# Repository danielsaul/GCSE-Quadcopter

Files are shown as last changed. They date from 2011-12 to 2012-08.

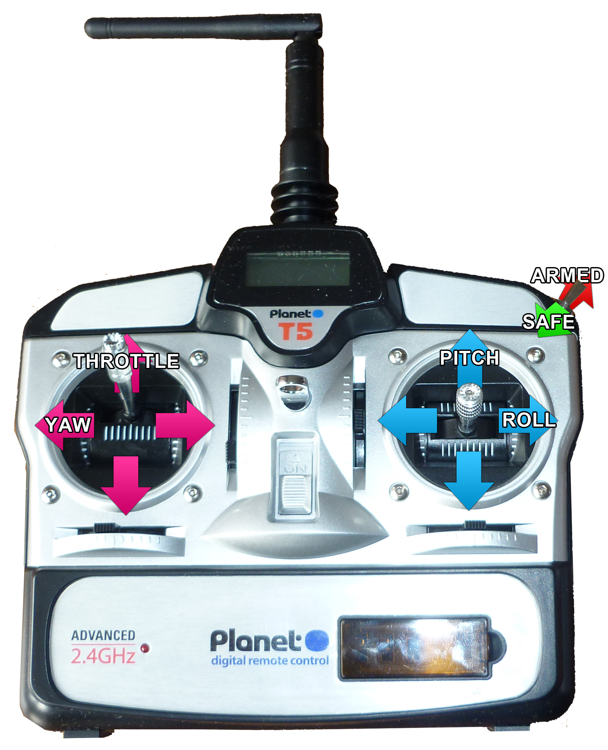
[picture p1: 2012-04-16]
Graphics/transmitterdiagram.jpg

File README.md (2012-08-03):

#GCSE Quadcopter - NOT FUNCTIONAL.
###Still here for historical purposes :)
#### � Copyright Daniel Saul

My GCSE Quadcopter project: the aim of which is to create a fully-functional, four rotored, remote control helicopter from scratch. 
Uses a custom designed PCB with an ATmega328 as the core microcontroller, using the arduino bootloader.

The IMU is made up of a 3-axis accelerometer, a 2-axis gyro and a 1-axis gyro to get 6 degrees of freedom. There is the possibility of extending this to include a magnetometer and GPS in the future.

There will also be an ultrasonic rangefinder on board for low-level altitude control.

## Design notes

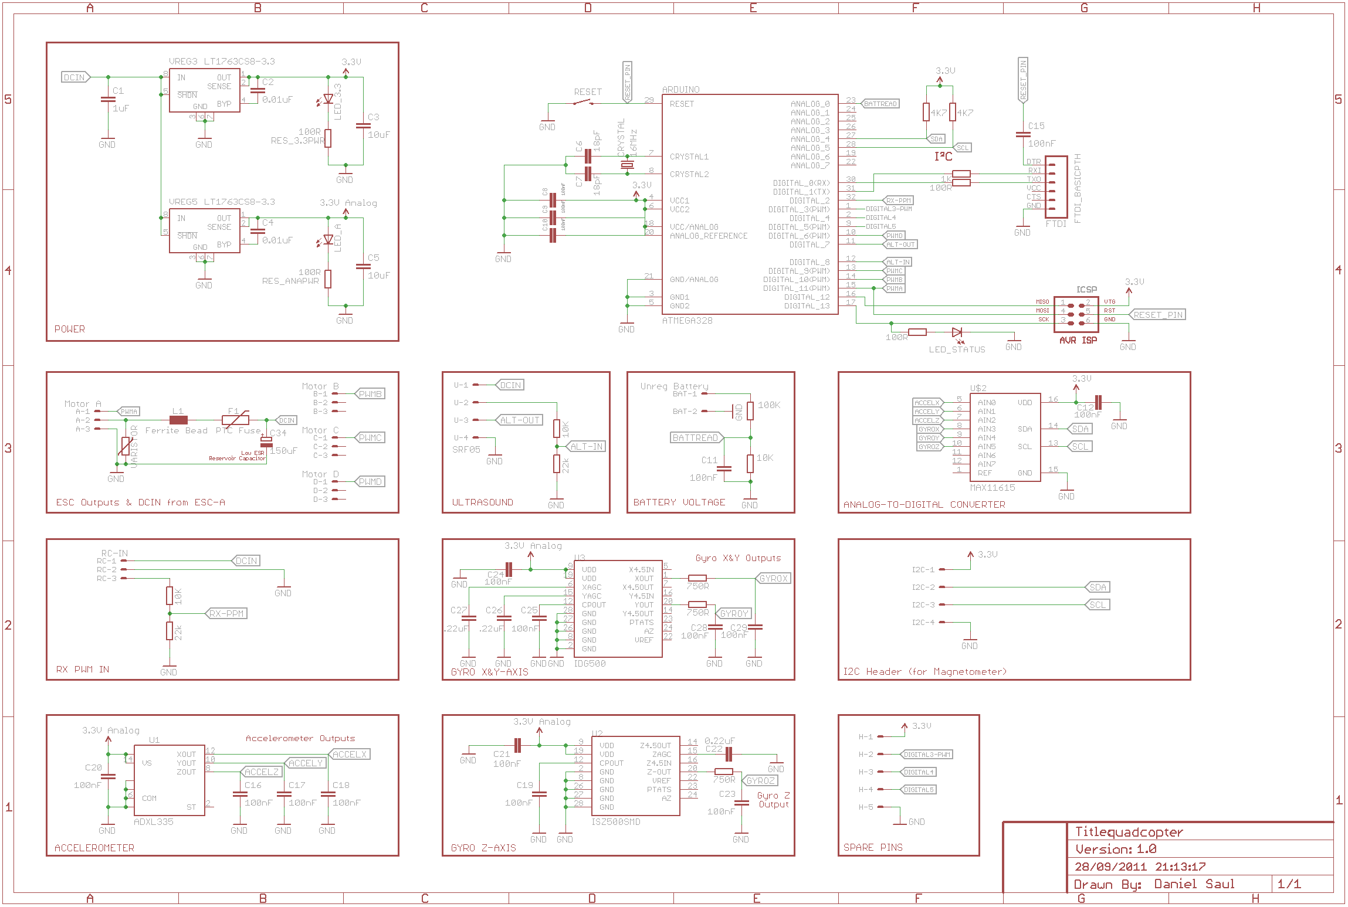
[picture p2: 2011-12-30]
PCB/schematic.png

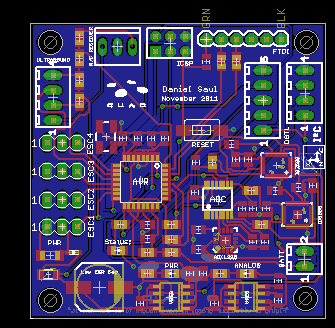
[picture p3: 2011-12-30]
PCB/pcb.png

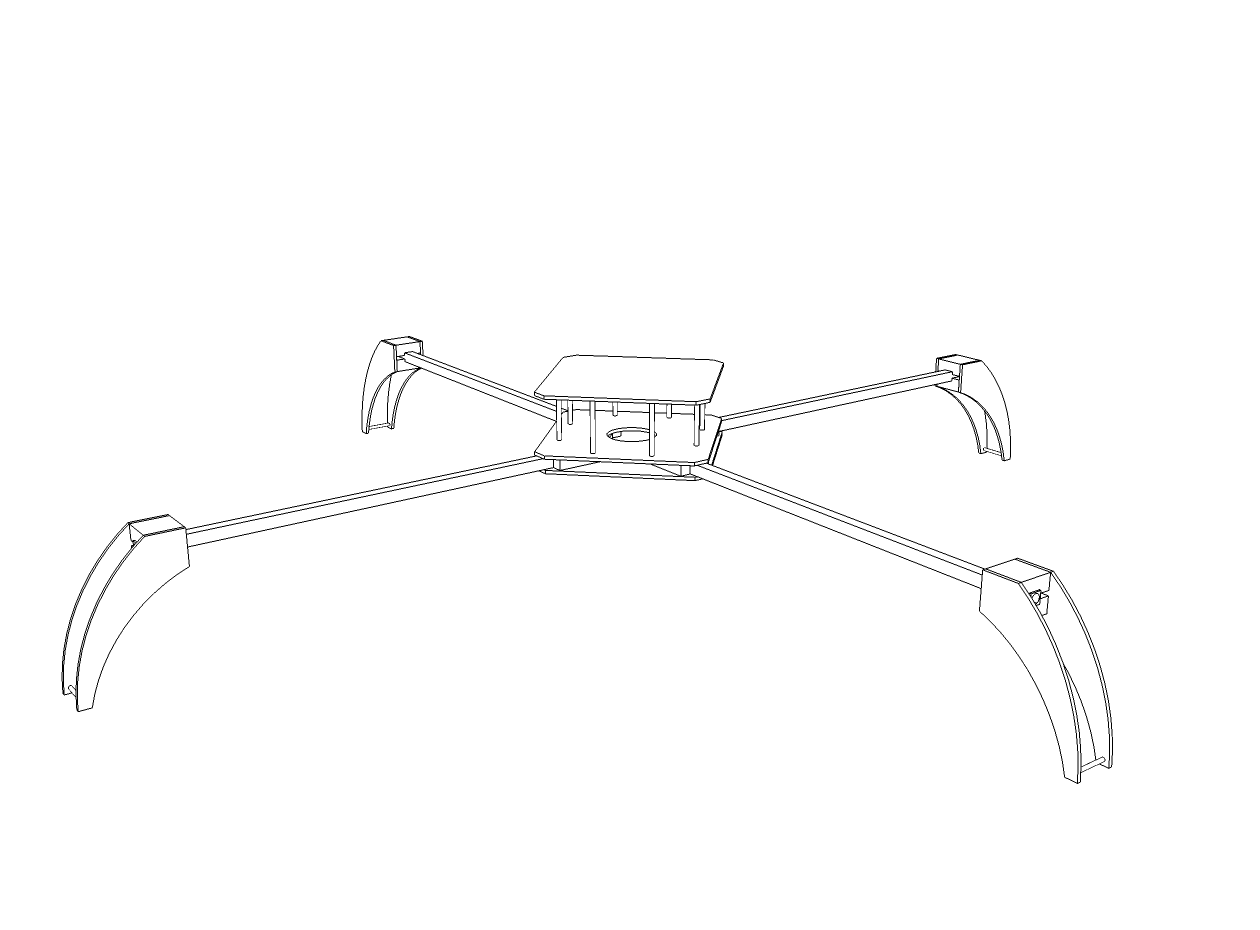
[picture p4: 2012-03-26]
Frame/line.png

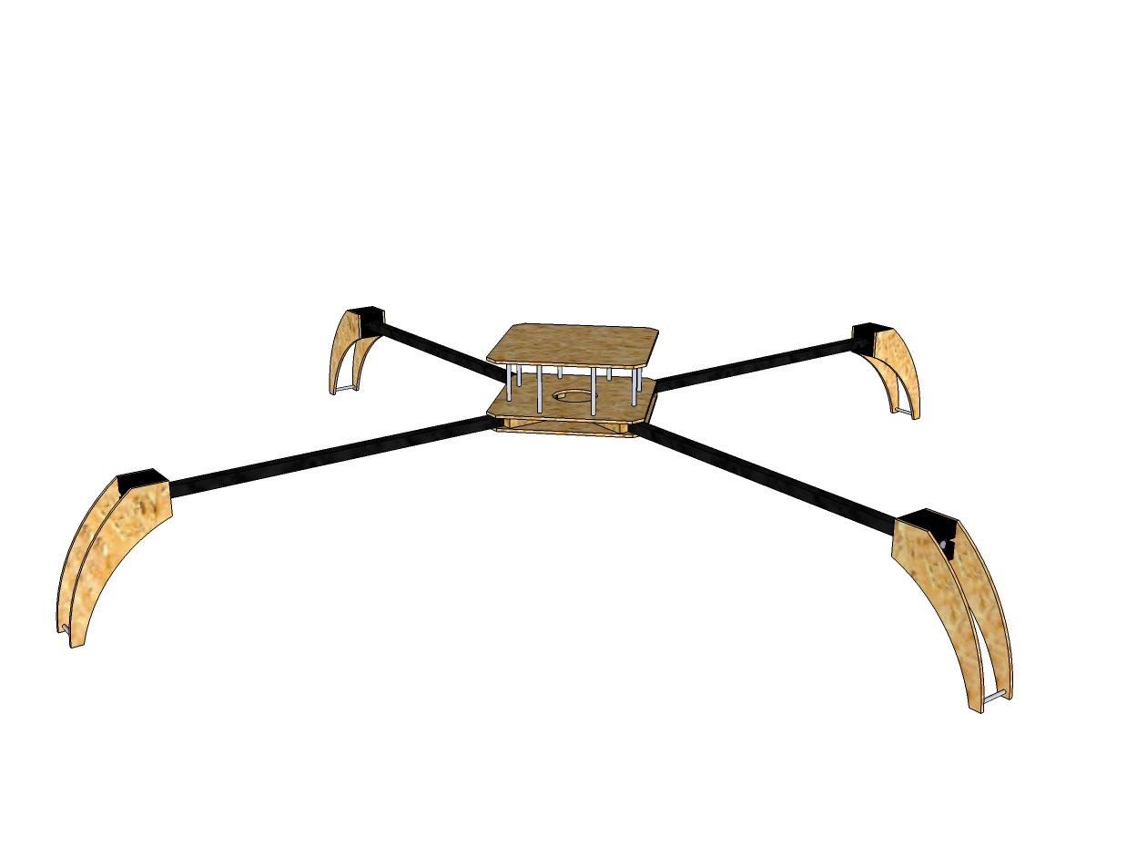
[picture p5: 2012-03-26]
Frame/shaded.png

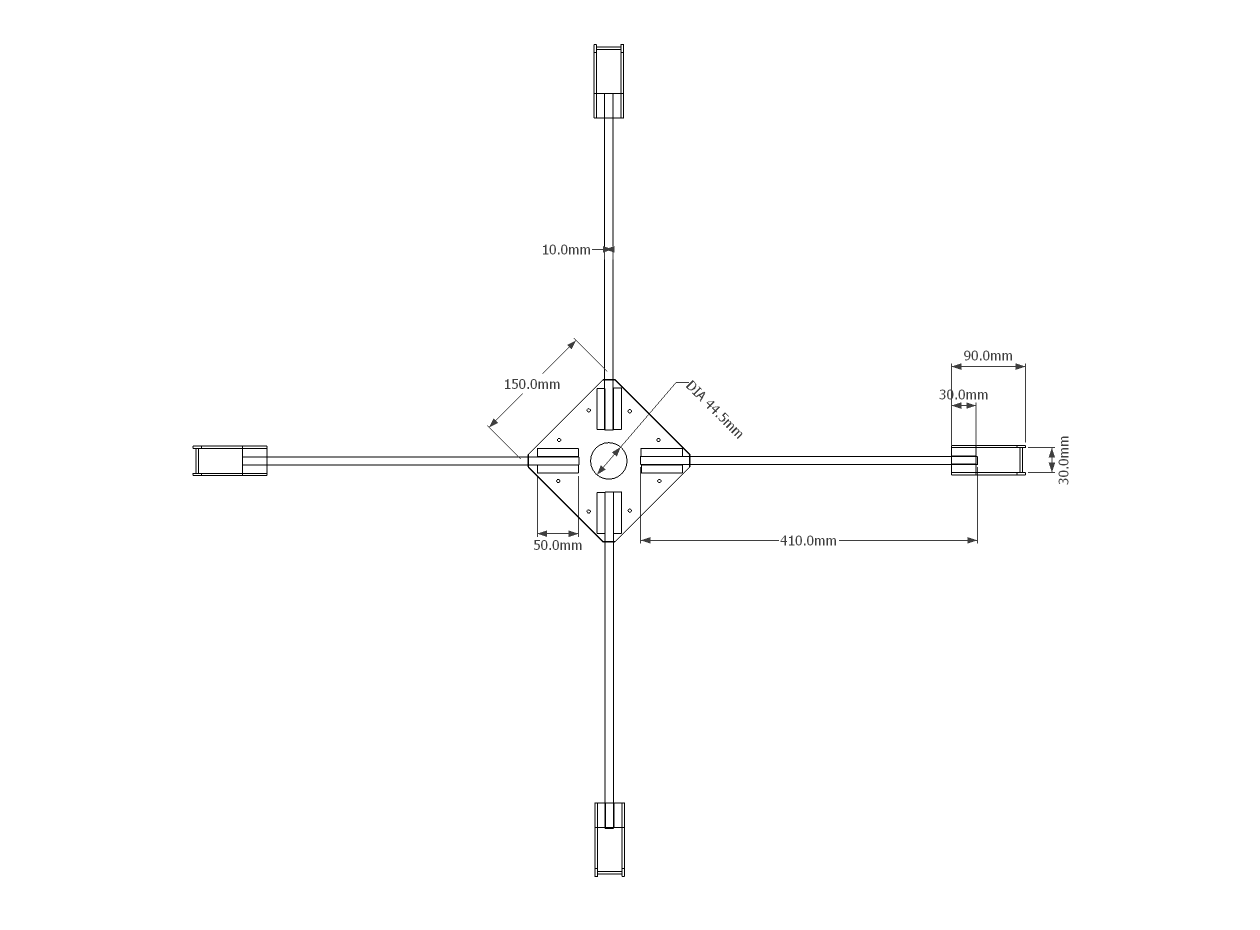
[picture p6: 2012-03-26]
Frame/line-top-dimensions.png

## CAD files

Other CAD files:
Frame/real.skp

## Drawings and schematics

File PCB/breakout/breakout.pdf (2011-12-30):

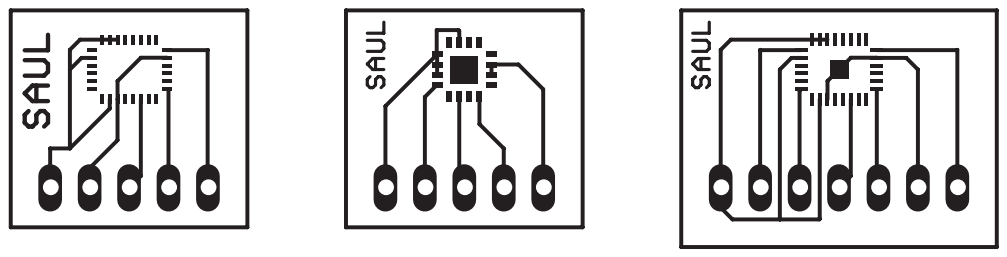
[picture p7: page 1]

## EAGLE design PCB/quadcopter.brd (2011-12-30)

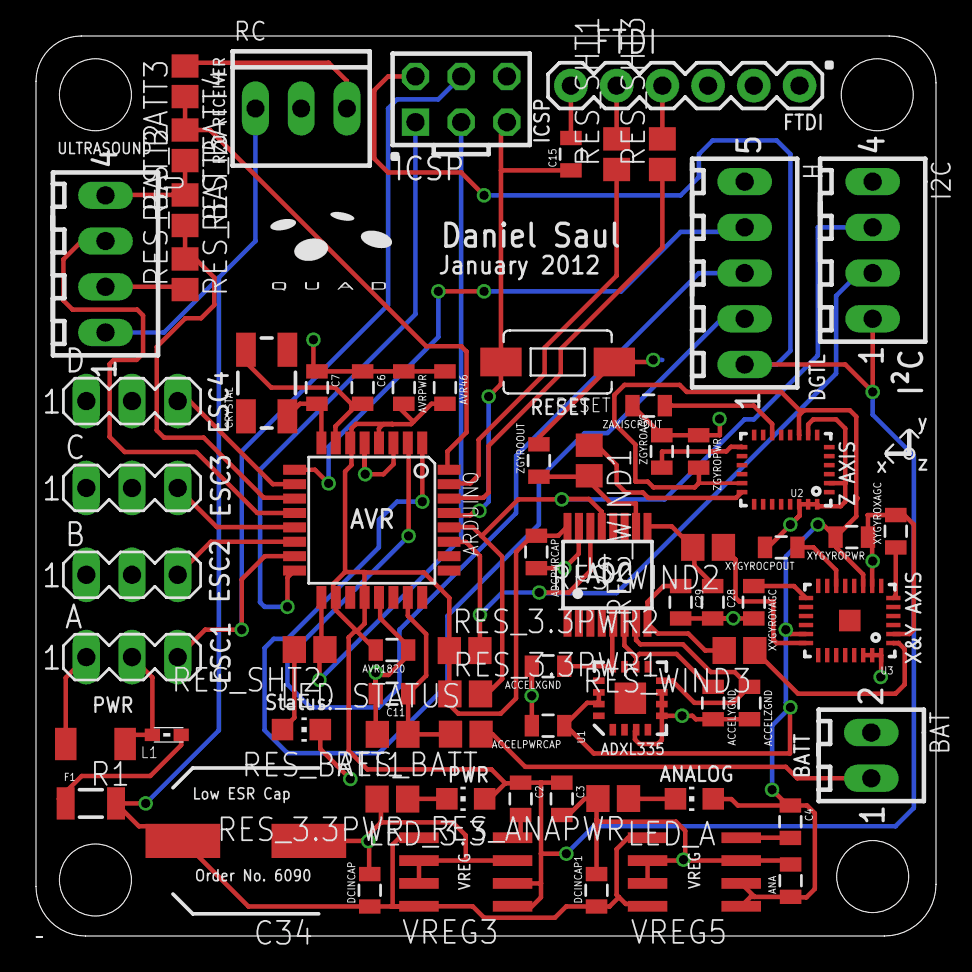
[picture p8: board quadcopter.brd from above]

Board: 2 copper layers, 50.0 x 50.0 mm, 72 parts (1 on the bottom side), 51 nets.

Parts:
A: Motor A; MA03-1
ACCELPWRCAP: 100nF; 0805
ACCELXGND: 100nF; 0805
ACCELYGND: 100nF; 0805
ACCELZGND: 100nF; 0805
ADCPWRCAP: 100nF; 0805
ANA: 10uF; 0805
ARDUINO: ATMEGA328; TQFP32-08
AVR46, AVR1820: 100nF; 0805
AVRPWR: 100nF; 0805
B: MA03-1
BAT: Unreg Battery; 6410-02
C: MA03-1
C2, C4: 0.01uF; 0805
C3: 10uF; 0805
C6, C7: 18pF; 0805
C11, C15, C28, C29: 100nF; 0805
C34: 150uF; SANYO-OSCON_SMD_E7
CRYSTAL: 16MHz; CRYSTAL-SMD-5X3
D: MA03-1
DCINCAP, DCINCAP1: 1uF; 0805
F1: PTC Fuse; PTC-1206
FTDI: FTDI_BASICPTH; FTDI_BASIC
H: 6410-05
I2C: 6410-04
ICSP: AVR-ISP-6
L1: Ferrite Bead; 0603
LED_3.3: red; CHIP-LED0805
LED_A: red; CHIP-LED0805
LED_STATUS: blue; CHIP-LED0805
R1: VARISTOR; CT/CN1206
RC: RC-IN; 22-23-2031
RESET: TACTILE-SWITCH-1101NE
RES_3.3PWR: 100R; R0805
RES_3.3PWR1, RES_3.3PWR2: 4K7; R0805
RES_ANAPWR: 100R; R0805
RES_BATT: 100K; R0805
RES_BATT1, RES_BATT2, RES_BATT4: 10K; R0805
RES_BATT3, RES_BATT5: 22k; R0805
RES_SHT1: 1K; R0805
RES_SHT2, RES_SHT3: 100R; R0805
RES_WIND1, RES_WIND2, RES_WIND3: 750R; R0805
U: SRF05; 6410-04
U1: ADXL335; LFCSP-16
U2: ISZ500SMD; QFN-28_6X8
U3: IDG500; SPARKFUN_IDG500
U$1: LOGO
U$2: MAX11615; QSOP16
VREG3, VREG5: LT1763CS8-3.3; SOIC8
XYGYROCPOUT: 100nF; 0805
XYGYROPWR: 100nF; 0805
XYGYROXAGC: .22uF; 0805
XYGYROYAGC: .22uF; 0805
ZAXISCPOUT: 100nF; 0805
ZGYROAGC: 0.22uF; 0805
ZGYROOUT: 100nF; 0805
ZGYROPWR: 100nF; 0805

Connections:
3.3V: ADCPWRCAP.1, ARDUINO.4, ARDUINO.6, ARDUINO.18, ARDUINO.20, AVR46.2, AVR1820.2, AVRPWR.2, C2.1, C3.1, H.1, I2C.1, ICSP.2, LED_3.3.A, RES_3.3PWR1.1, RES_3.3PWR2.1, U$2.16, VREG3.1, VREG3.2
3.3VANALOG: ACCELPWRCAP.1, ANA.1, C4.1, LED_A.A, U1.14, U1.15, U2.9, U2.19, U3.9, U3.19, VREG5.1, VREG5.2, XYGYROPWR.2, ZGYROPWR.2
16: ARDUINO.16, ICSP.1
ACCELX: ACCELXGND.1, U1.12, U$2.5
ACCELY: ACCELYGND.1, U1.10, U$2.6
ACCELZ: ACCELZGND.1, U1.8, U$2.7
ALT-IN: ARDUINO.11, RES_BATT2.2, RES_BATT3.1
ALT-OUT: ARDUINO.12, U.3
BATTREAD: ARDUINO.23, C11.1, RES_BATT.2, RES_BATT1.1
DCIN: C34.+, DCINCAP.1, DCINCAP1.1, F1.2, RC.1, U.1, VREG3.5, VREG3.8, VREG5.5, VREG5.8
DIGITAL3-PWM: ARDUINO.1, H.2
DIGITAL4: ARDUINO.2, H.3
DIGITAL5: ARDUINO.9, H.4
GND: A.1, ACCELPWRCAP.2, ACCELXGND.2, ACCELYGND.2, ACCELZGND.2, ADCPWRCAP.2, ANA.2, ARDUINO.3, ARDUINO.5, ARDUINO.21, AVR46.1, AVR1820.1, AVRPWR.1, BAT.2, C3.2, C6.1, C7.1, C11.2, C28.2, C29.2, C34.-, DCINCAP.2, DCINCAP1.2, FTDI.GND, H.5, I2C.4, ICSP.6, LED_STATUS.C, R1.2, RC.2, RESET.P$1, RES_3.3PWR.2, RES_ANAPWR.2, RES_BATT1.2, RES_BATT3.2, RES_BATT5.2, U.4, U1.3, U1.5, U1.6, U1.7, U2.2, U2.8, U2.26, U2.27, U2.28, U3.2, U3.8, U3.26, U3.27, U3.28, U$2.15, VREG3.3, VREG3.6, VREG3.7, VREG5.3, VREG5.6, VREG5.7, XYGYROCPOUT.2, XYGYROPWR.1, XYGYROXAGC.2, XYGYROYAGC.2, ZAXISCPOUT.2, ZGYROAGC.2, ZGYROOUT.2, ZGYROPWR.1
GYROX: C29.1, RES_WIND3.2, U$2.8
GYROY: C28.1, RES_WIND2.2, U$2.9
GYROZ: RES_WIND1.2, U$2.10, ZGYROOUT.1
unnamed: C4.2, VREG5.4
unnamed: BAT.1, RES_BATT.1
unnamed: LED_3.3.C, RES_3.3PWR.1
unnamed: C2.2, VREG3.4
unnamed: LED_A.C, RES_ANAPWR.1
unnamed: ARDUINO.7, C6.2, CRYSTAL.3
unnamed: ARDUINO.8, C7.2, CRYSTAL.1
unnamed: FTDI.RXI, RES_SHT1.2
unnamed: FTDI.TXO, RES_SHT3.2
unnamed: C15.2, FTDI.DTR
unnamed: F1.1, L1.2
unnamed: RES_BATT2.1, U.2
unnamed: ARDUINO.17, ICSP.3, RES_SHT2.1
unnamed: LED_STATUS.A, RES_SHT2.2
unnamed: RC.3, RES_BATT4.1
unnamed: U2.15, ZGYROAGC.1
unnamed: U2.12, ZAXISCPOUT.1
unnamed: RES_WIND1.1, U2.20
unnamed: U3.15, XYGYROYAGC.1
unnamed: U3.12, XYGYROCPOUT.1
unnamed: U3.6, XYGYROXAGC.1
unnamed: RES_WIND2.1, U3.20
unnamed: RES_WIND3.1, U3.1
PWMA: A.3, ARDUINO.15, ICSP.4
PWMB: ARDUINO.14, B.3
PWMC: ARDUINO.13, C.3
PWMD: ARDUINO.10, D.3
RC-IN1: ARDUINO.31, RES_SHT1.1
RC-IN2: ARDUINO.30, RES_SHT3.1
RESET_PIN: ARDUINO.29, C15.1, ICSP.5, RESET.P$2
RX-PPM: ARDUINO.32, RES_BATT4.2, RES_BATT5.1
S: A.2, L1.1, R1.1
SCL: ARDUINO.28, I2C.3, RES_3.3PWR1.2, U$2.13
SDA: ARDUINO.27, I2C.2, RES_3.3PWR2.2, U$2.14

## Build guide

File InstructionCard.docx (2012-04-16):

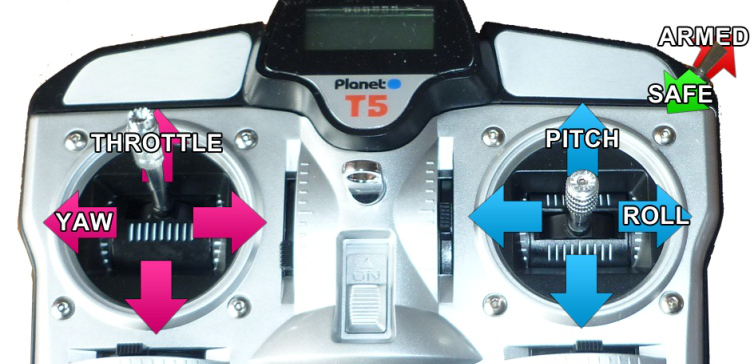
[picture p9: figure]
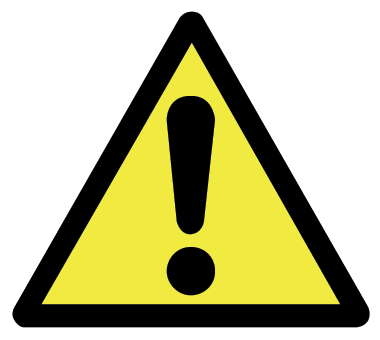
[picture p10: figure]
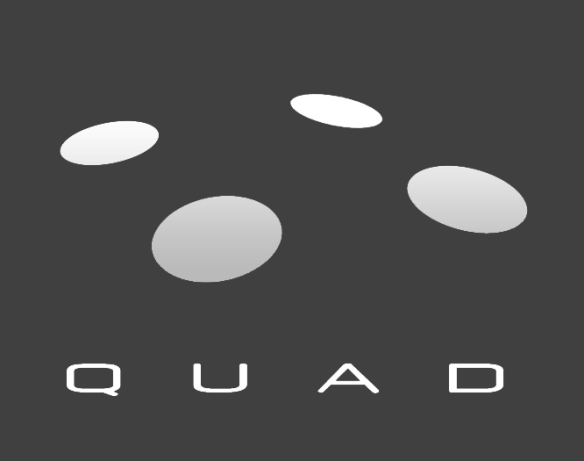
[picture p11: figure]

Instructions for Use

1. Turn on the transmitter, ensuring the throttle is in the lowest position and the motor switch is set to 'safe'.
2. Plug the battery into the QuadCopter, place it on flat and level ground before standing back.
3. Calibrate the sensors by pulling both sticks to the bottom, outside corners.
4. When ready to fly, set the motor switch to the 'armed' position and slowly increase the 'throttle' to rise.

Once hovering, to move forwards and backwards, alter the 'pitch'. To move left and right, alter the 'roll'. To turn on the spot, alter the 'yaw'. Finally, to ascend or descend further, alter the 'throttle'.

SAFETY INFORMATION

The QuadCopter should

only be flown outside, in an open space in good weather, with little wind and must not be flown close to, or above, other people.

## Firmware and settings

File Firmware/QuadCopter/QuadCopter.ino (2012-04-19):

/*
  QuadCopter - GCSE Electronic Products
  Daniel Saul - www.DanSaul.co.uk
  (C) Copyright 2011. All Rights Reserved.
 
  Arduino-based Quadcopter Control System
 
  #File     : QuadCopter.pde
  #Author   : Daniel Saul

 */

// Include various header files
#include "QuadCopter.h"
#include "adc.h"
#include "pid.h"
#include "receiver.h"
#include "motors.h"
#include "accel.h"
#include "gyro.h"

/////////////////////////////////
// Main Program Initialisation //
// //////////////////////////////
void setup(){

    // Status LED
    pinMode(STATUS_LED, OUTPUT);
    digitalWrite(STATUS_LED, HIGH);
    delay(500);
    digitalWrite(STATUS_LED, LOW);

    // Begin Serial to Computer, if enabled
    if (SERIAL_ENABLED) {
        Serial.begin(BAUD_RATE);
        Serial.println("Quadcopter - GCSE Electronic Products");
        Serial.println("Daniel Saul - 2012 \n");
    }
    
    setupReceiver();    
    setupADC();
    setupMotors();
    setupGyro();
    setupAccel();

    prevTime = micros();
}

void loop(){
    
    loopTime = micros();
    diffTime = loopTime - prevTime;

    // 100Hz Loop - runs 100 times a second
    if(diffTime >= 10000) {
        diffTimeSecs = diffTime / 1000000.0;
        
        // Read Sensors
        readADC();
        measureGyro();
        measureAccel();

        calculateKinematics(gyroRate[XAXIS],gyroRate[YAXIS],gyroRate[ZAXIS],filteredAccel[XAXIS],filteredAccel[YAXIS],filteredAccel[ZAXIS],0.0,0.0,0.0,diffTimeSecs);


        //Motor Stuff
        if(!GYRO_MODE){
            float rollAccelPID = processPID((rxRaw[1]-1500) * 0.0015, kinematicsAngle[XAXIS], &pidstuff[3]);
            float pitchAccelPID = processPID((rxRaw[0]-1500) * 0.0015, -kinematicsAngle[YAXIS], &pidstuff[4]);
            rollAxis = processPID(rollAccelPID, gyroRate[XAXIS]*1.2, &pidstuff[5]);
            pitchAxis = processPID(pitchAccelPID, gyroRate[YAXIS]*1.2, &pidstuff[6]);
        }else{
            rollAxis = processPID((rxRaw[1]-1500) * 0.005, gyroRate[XAXIS]*0.8, &pidstuff[0]);
            pitchAxis = processPID((rxRaw[0]-1500) * 0.005, gyroRate[YAXIS]*0.8, &pidstuff[1]);
        }

        motorSpeed[MOTOR_A] = rxRaw[2] - pitchAxis;
        motorSpeed[MOTOR_C] = rxRaw[2] + pitchAxis;
        motorSpeed[MOTOR_B] = rxRaw[2] - rollAxis;
        motorSpeed[MOTOR_D] = rxRaw[2] + rollAxis;

       for(byte motor = 0; motor < 4; motor++){
            motorSpeed[motor] = constrain(motorSpeed[motor], 1100, 2000);
            if(rxRaw[2] < 1100){
                motorSpeed[motor] = 1100;
            }
       }

        checkRXCommands();
        if(!motorsArmed){
            setMotors(MOTOR_OFFSPEED,MOTOR_OFFSPEED,MOTOR_OFFSPEED,MOTOR_OFFSPEED);
        }

        updateMotors();

        prevTime = loopTime;
    }

}

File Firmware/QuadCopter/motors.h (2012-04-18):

/*
  QuadCopter - GCSE Electronic Products
  Daniel Saul - www.DanSaul.co.uk
  (C) Copyright 2011/2012. All Rights Reserved.
 
  Arduino-based Quadcopter Control System
 
  #File     : motors.h
  #Author   : Daniel Saul

 */

#ifndef MOTORS_H
#define MOTORS_H

// Include necessary header files
#include "Arduino.h"
#include "QuadCopter.h"
#include "Servo.h"


//Declare functions
void setupMotors();
void updateMotors();
void setMotors();

//Declare Variables
Servo motorA;
Servo motorB;
Servo motorC;
Servo motorD;

int motorSpeed[4] = { MOTOR_OFFSPEED, MOTOR_OFFSPEED, MOTOR_OFFSPEED, MOTOR_OFFSPEED };

////////////////////
//Actual functions//
////////////////////

void setupMotors(){

    pinMode(MOTORA_PIN, OUTPUT);
    digitalWrite(MOTORA_PIN, LOW);
    pinMode(MOTORB_PIN, OUTPUT);
    digitalWrite(MOTORB_PIN, LOW);
    pinMode(MOTORC_PIN, OUTPUT);
    digitalWrite(MOTORC_PIN, LOW);
    pinMode(MOTORD_PIN, OUTPUT);
    digitalWrite(MOTORD_PIN, LOW);



    motorA.attach(MOTORA_PIN);
    motorB.attach(MOTORB_PIN);
    motorC.attach(MOTORC_PIN);
    motorD.attach(MOTORD_PIN);

    digitalWrite(STATUS_LED,HIGH);              //Flash Status LED
    delay(50);
    digitalWrite(STATUS_LED,LOW);

    updateMotors();
        
    if (SERIAL_ENABLED){
        Serial.println("Motors: Setup Complete.");
        Serial.println("Motors: Disarmed.");
    }

}

void setMotors(int a, int b, int c, int d){

    motorSpeed[MOTOR_A] = a;
    motorSpeed[MOTOR_B] = b;
    motorSpeed[MOTOR_C] = c;
    motorSpeed[MOTOR_D] = d;

}

void updateMotors(){

    motorA.writeMicroseconds(motorSpeed[MOTOR_A]);
    motorB.writeMicroseconds(motorSpeed[MOTOR_B]);
    motorC.writeMicroseconds(motorSpeed[MOTOR_C]);
    motorD.writeMicroseconds(motorSpeed[MOTOR_D]);

}


#endif

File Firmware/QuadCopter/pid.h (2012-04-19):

/*
  QuadCopter - GCSE Electronic Products
  Daniel Saul - www.DanSaul.co.uk
  (C) Copyright 2011. All Rights Reserved.
 
  Arduino-based Quadcopter Control System
 
  #File     : pid.h
  #Author   : Daniel Saul

 */

#ifndef PID_H
#define PID_H

//Include necessary header files
#include "Arduino.h"
#include "QuadCopter.h"

//Declare functions
float processPID(float target, float current, struct PIDvariables *pid);

//Declare Variables
struct PIDvariables{
    float Pgain;
    float Igain;
    float Dgain;
    float previous;
    float prevtime;
    float accumulatedError;
    float Ilimit;
} pidstuff[8] = { 
    { 100.0, 0.0, -300.0, 0.0, 0.0, 0.0, 1000.0 }, //PID[0]  GYRO_MODE  ROLL
    { 100.0, 0.0, -300.0, 0.0, 0.0, 0.0, 1000.0 }, //PID[1]  GYRO_MODE  PITCH
    { 200.0, 5.0, 0.0, 0.0, 0.0, 0.0, 1000.0 }, //PID[2]  GYRO_MODE  YAW
    { 4.0, 0.0, 0.0, 0.0, 0.0, 0.0, 0.375 }, //PID[3]  STABLE     ROLL
    { 4.0, 0.0, 0.0, 0.0, 0.0, 0.0, 0.375 }, //PID[4]  STABLE     PITCH
    { 100.0, 0.0, -300.0, 0.0, 0.0, 0.0, 1000.0 }, //PID[5]  STABLEGYRO ROLL
    { 100.0, 0.0, -300.0, 0.0, 0.0, 0.0, 1000.0 },//PID[6]  STABLEGYRO PITCH
    { 3.0, 0.1, 0.0, 0.0, 0.0, 0.0, 1000.0 }};//PID[7]  HEADING HOLD




// Proportional Integral Derivative Controller

float processPID(float target, float current, struct PIDvariables *pid){

    float error = target - current;

    float timediff = (loopTime - pid->prevtime) / 1000000.0; //Convert microseconds to seconds
    pid->prevtime = loopTime;

    pid->accumulatedError += error * timediff;
    constrain(pid->accumulatedError, -pid->Ilimit, pid->Ilimit);

    int Pterm = error * pid->Pgain;
    int Iterm = pid->accumulatedError * pid->Igain;
    int Dterm = ((current - pid->previous) * pid->Dgain) / (timediff * 100);    
    
    pid->previous = current;

    return Pterm + Iterm + Dterm;

}

void zeroAccumulatedError(){
    for(byte i = 0; i <= 6; i++){
        pidstuff[i].accumulatedError = 0;
        pidstuff[i].prevtime = loopTime;
    }
}

#endif

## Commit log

2011-09-21 Finished schematic
    [quadcopter.sch]
2011-12-30 Updated Repo
    [ArduPilotMegaShield_F_v141 (4).sch, ArduPilotMega_v141.sch, quadcopter.sch]
2012-01-06 PCB development in project folder
2012-01-25 Receiver interrupt code done
2012-02-17 Continued with receiver & fixed bits
    [QuadCopter.h, QuadCopter.ino, pid.h]
2012-03-26 Frame Sketchup done. ADC firmware added.
2012-04-03 Accel Calibration and measurement routines written
2012-04-03 Added necessary libraries. Fixed accel, changed variable types to float
    [QuadCopter.ino, accel.h, gyro.h]
2012-04-04 Gyro calibration routine written
2012-04-04 Measure gyro written - can now get radians/s for each axis
2012-04-08 Altered PID, gyroRate is ADC value temporarily & trying to get vaguely level hover
2012-04-13 Updated project folder. Gyro-only throttle up/down firmware done.
2012-04-14 Storing calibrated sensor offsets in EEPROM.
2012-04-15 Added calibration command from tx & started sorting 100Hz loop
2012-04-15 Fourth Order Filter from AeroQuad implemented
2012-04-17 Started motor control bits in 100Hz loop
2012-04-18 PID, Main loop, project folder etc.
2012-04-19 Squashed another bug.. missing '&'s, grrr
    [QuadCopter.ino]
2012-04-20 Fixed some type conversions on readadc, added yawhold.h
    [gyro.h]
